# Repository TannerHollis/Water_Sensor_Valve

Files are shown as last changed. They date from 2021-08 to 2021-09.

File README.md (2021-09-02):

# Water Sensor Valve
 This project mimics the operation of a "Water Cop". While commercial use of this device is expensive, a simple cheap clone can be replicated for a mere dollars.
 
## Water Sensor
The water sensor is a simple wheatstone bridge with one leg of the resistor divider being the exposed metal strips in the probe. Due to variation in the installation of the product, the probe's resistivity will change. Using a wide variety of different possible probe gaps, the wheatstone bridge is configurable for up to 15 different resistor combinations. See [total_resistor_combinations.txt](https://github.com/TannerHollis/Water_Sensor_Valve/blob/main/Water_Valve_Calculations/total_resistor_combinations.txt) for all possible combinations. The purpose of this configuration is to accomodate for a wide range of possible probe resistivities.

A "dirty" or water typically found with contamination in it widely varies in it's resistivity, or it's ability to conduct electricity. Since the resistivity of air is magnitudes larger than the resistivity of water, the effect on the probes open air contacts can be ignored for the theoretical calculations. 

Contaminated water has a resitivity typically between 20 to 2000 Ohms. To calculate the theoretical resistance between two electrical wires submerged in water, one must utilize the resistance formula.

	R = p L / A
 
This device is meant to be used with a probe with a small 2mm gap and approximately 31um^2 of exposed contacts on the probe, which when submerged in conductive water yields a theoretical maximum resistance of ~127 kOhms. Tolerances must be added to assure the proper resistivity is measured. In this scenario, we would recommend using a setting of 84.777 kOhms which corresponds to jumping resistors R3 and R4 corresponding to 127 and 255 kOhm resistors. At this set point, any measured resistance below the threshold of 84.777 kOhms will trigger the closing of the valve and sounding of the alarm.

Adjustments may be needed for more sensitivity or security. For more sensitivity, refer to the resistor combination file and choose the next highest setting. For more security,  choose the next lowest setting. Continue to do so until the desired operation is achieved. 

## Custom Setting Attachment
This add-on is a customizable attachment that is configurable with either the use the included potentiometer or the solderable resistor footprint. With the included mosfet, an external controller can be attached and control the Water Sensor Valve using the connections with the use of the included external mosfet.

- [X] Test and verify first revision
- [X] Verify alarm and valve operation
- [ ] Design and print custom device housing
- [ ] Create custom setting attachment
- [ ] Control device with custom setting attachment using MCU
- [ ] Setup configurable custom setting attachement using potentiometer

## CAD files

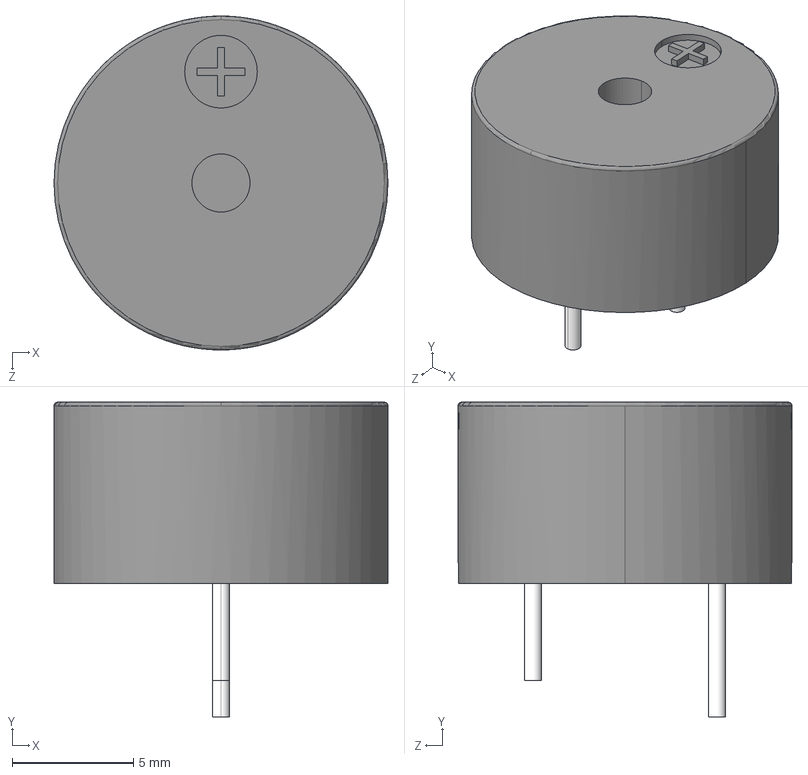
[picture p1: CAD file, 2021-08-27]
Water_Valve_Sensor/Parts/CUI_DEVICES_CPI-1375IC-80T.step
13.8 x 13.0 x 13.8 mm

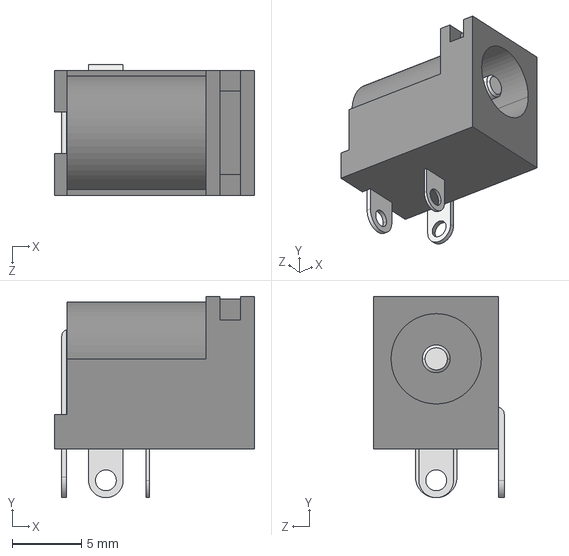
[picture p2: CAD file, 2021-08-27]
Water_Valve_Sensor/Parts/CUI_DEVICES_PJ-002A.step
14.4 x 14.5 x 9.40 mm

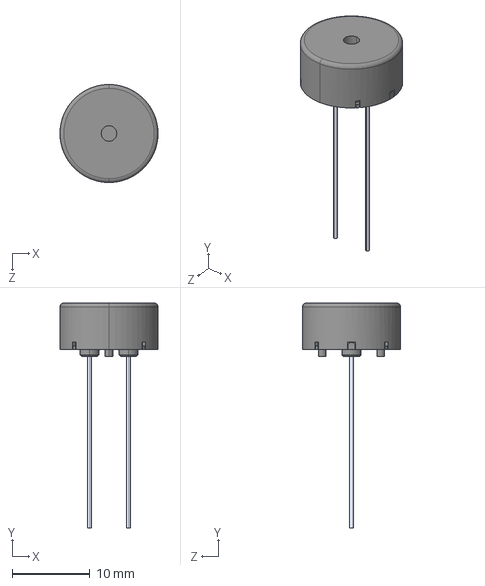
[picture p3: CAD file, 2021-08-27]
Water_Valve_Sensor/Parts/PKM13EPYH4000-A0.step
12.6 x 28.9 x 12.6 mm

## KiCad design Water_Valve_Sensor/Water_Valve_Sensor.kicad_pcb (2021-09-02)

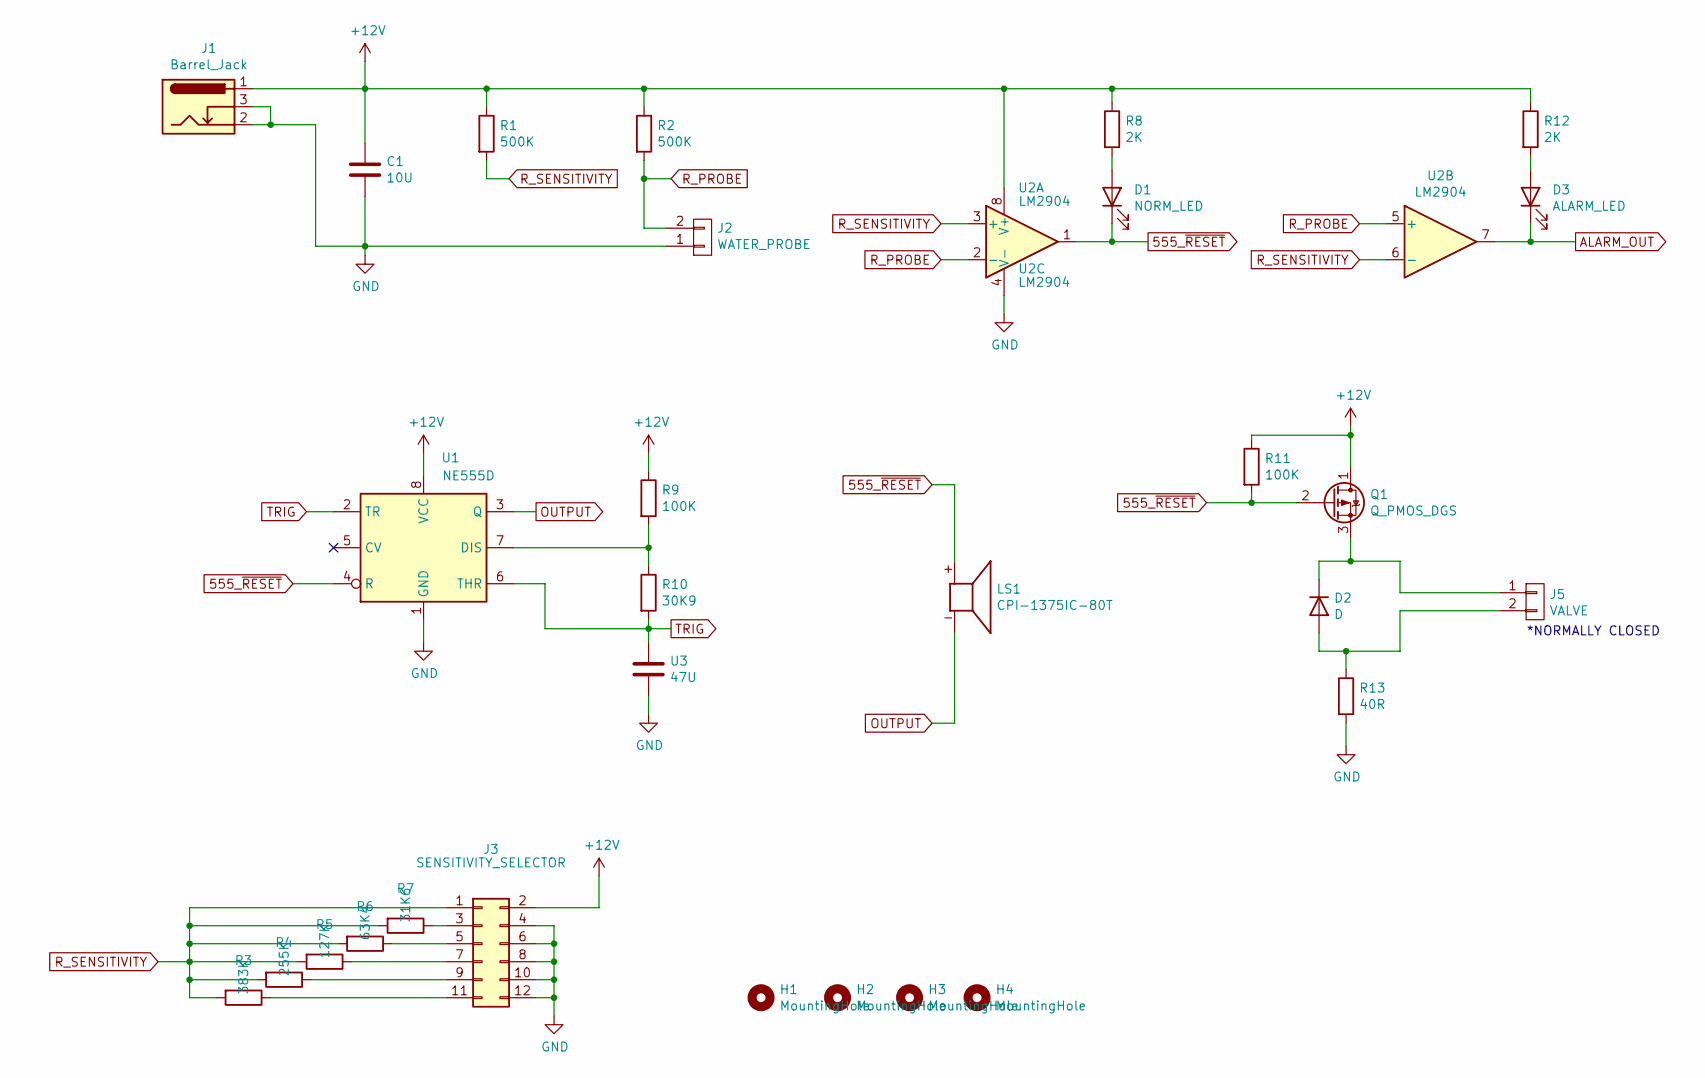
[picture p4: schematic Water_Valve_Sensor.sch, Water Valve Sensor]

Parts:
C1: 10U; CP_Radial_D5.0mm_P2.00mm
D1: NORM_LED; LED_D3.0mm
D2: D; D_DO-15_P10.16mm_Horizontal
D3: ALARM_LED; LED_D3.0mm
H1, H2, H3, H4: MountingHole; MountingHole_2.5mm_Pad_TopBottom
J1: Barrel_Jack; PJ-002A
J2: WATER_PROBE; PinHeader_1x02_P2.54mm_Horizontal
J3: SENSITIVITY_SELECTOR; PinHeader_2x06_P2.54mm_Vertical
J5: VALVE; PinHeader_1x02_P2.54mm_Horizontal
LS1: CPI-1375IC-80T; CUI_CPI-1375IC-80T; PARTREV 1.0
Q1: Q_PMOS_DGS; TO-92
R1, R2: 500K; R_Axial_DIN0207_L6.3mm_D2.5mm_P7.62mm_Horizontal
R3: 383K; R_Axial_DIN0207_L6.3mm_D2.5mm_P7.62mm_Horizontal
R4: 255K; R_Axial_DIN0207_L6.3mm_D2.5mm_P7.62mm_Horizontal
R5: 127K; R_Axial_DIN0207_L6.3mm_D2.5mm_P7.62mm_Horizontal
R6: 63K4; R_Axial_DIN0207_L6.3mm_D2.5mm_P7.62mm_Horizontal
R7: 31K6; R_Axial_DIN0207_L6.3mm_D2.5mm_P7.62mm_Horizontal
R8, R12: 2K; R_Axial_DIN0207_L6.3mm_D2.5mm_P7.62mm_Horizontal
R9, R11: 100K; R_Axial_DIN0207_L6.3mm_D2.5mm_P7.62mm_Horizontal
R10: 30K9; R_Axial_DIN0207_L6.3mm_D2.5mm_P7.62mm_Horizontal
R13: 40R; R_Axial_DIN0207_L6.3mm_D2.5mm_P7.62mm_Horizontal
U1: NE555D; SOIC-8_3.9x4.9mm_P1.27mm
U2: LM2904; SOIC-8_3.9x4.9mm_P1.27mm
U3: 47U; CP_Radial_D5.0mm_P2.00mm

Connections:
555_~RESET~: D1.1 (K), LS1.P, Q1.2 (G), R11.2, U1.4 (R), U2.1
+12V: C1.1, J1.1, J3.2, Q1.1 (D), R1.1, R2.1, R8.1, R9.1, R11.1, R12.1, U1.8 (VCC), U2.8 (V+)
ALARM_OUT: D3.1 (K), U2.7
GND: C1.2, J1.2, J1.3, J2.1, J3.4, J3.6, J3.8, J3.10, J3.12, R13.2, U1.1 (GND), U2.4 (V-), U3.2
unnamed: D1.2 (A), R8.2
unnamed: D2.1 (K), J5.1, Q1.3 (S)
unnamed: D2.2 (A), J5.2, R13.1
unnamed: D3.2 (A), R12.2
unnamed: J3.3, R7.1
unnamed: J3.5, R6.1
unnamed: J3.7, R5.1
unnamed: J3.9, R4.1
unnamed: J3.11, R3.1
unnamed: R9.2, R10.1, U1.7 (DIS)
OUTPUT: LS1.N, U1.3 (Q)
R_PROBE: J2.2, R2.2, U2.2 (-), U2.5 (+)
R_SENSITIVITY: J3.1, R1.2, R3.2, R4.2, R5.2, R6.2, R7.2, U2.3 (+), U2.6 (-)
TRIG: R10.2, U1.2 (TR), U1.6 (THR), U3.1

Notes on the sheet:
*NORMALLY CLOSED

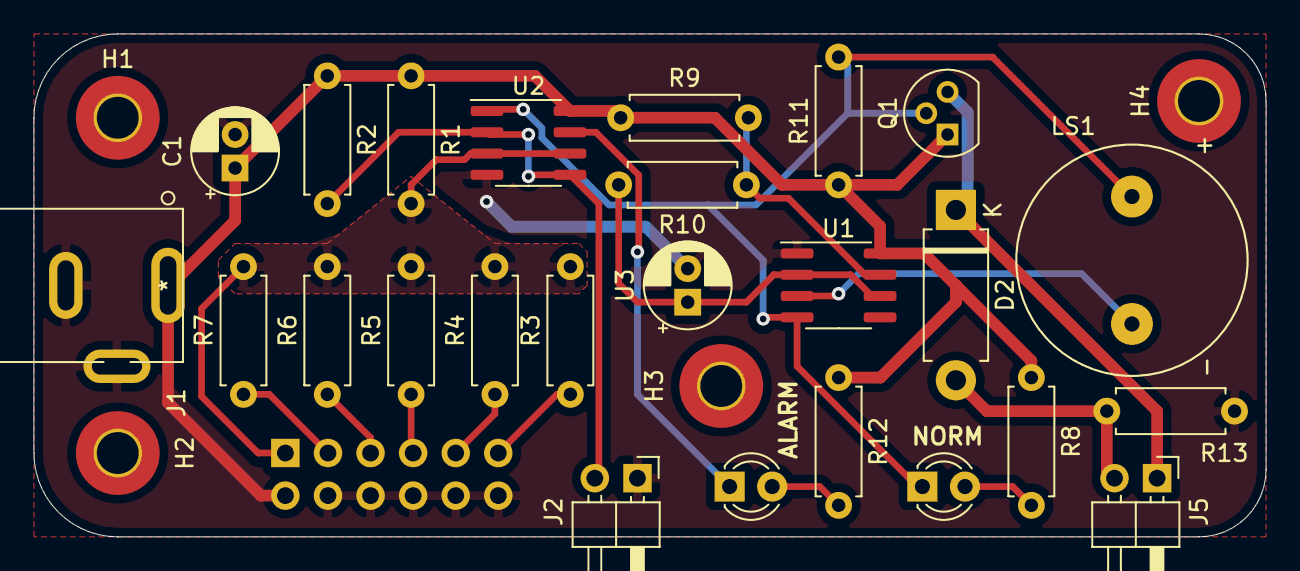
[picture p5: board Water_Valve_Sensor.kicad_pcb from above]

Board: 2 copper layers, 73.5 x 30.0 mm, 30 parts (1 on the bottom side), 18 nets.

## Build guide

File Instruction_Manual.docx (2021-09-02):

# Water Sensor Valve Instructions

Offset Power, Inc.

### Phone: (704) - 999 -3983

Email: hollis.tanner@gmail.com

This device is intended to be used in areas where access to leaking waterlines or faucets is not easily accessible. When the device’s probes encounter water or a conductive liquid, the device will alarm and close the water valve, preventing water damage to the surrounding area. Included in this package are the following contents:

| Item | Description
1x | Wall adapter | 12V, 6W AC-DC Wall Adapter
1x | Water Sensor Device | Water Sensor Device
1x | Solenoid Valve | 12V, 250mA Normally Closed (NC) Valve
1x | Water Probe | Water Sensor Probe, 2mm Gap
5x | Sensitivity Jumpers | Sensitivity Selector Jumpers

# Easy Setup Instructions

## Ensure the normal operation of the device

1. Locate a nearby wall outlet nearest to the desired location and plug-in the wall adapter.
2. Connect the barrel jack into the device and the green light should light to indicate that the device is powered-on and working normally.
3. Connect the valve into the device before installing the water valve in place.
4. Connect the water probe into the device and keep the probe’s sheaths on.
5. If not connected, connect a single Sensitivity Jumper in position 1 (Fig. 1).

## Test the Device

1. Remove the probe’s rubber sheath and test the probe by dipping it into water or by wetting one’s finger tips and squeezing the probe.
2. The device’s normal LED should turn-off and the alarm LED should turn-on.
3. The valve should close and the alarm should sound.
4. The alarm will sound for approximately 1 second and turn-off for 3.5 seconds.
5. If this sequence is not heard, continue to sensitivity tuning is properly done before continuing troubleshooting.

## Sensitivity Tuning

This device is intended to operate in a wide variety of conditions. For instance, placing this device in a damp and cool place may cause a misoperation due to very high air humidty. To ensure proper functionality, please follow these steps:

1. Start with a single Sensitivity Jumper in position 1 (Fig. 1)
2. Test the probe by dipping it into water or squeezing between wet fingers.
3. Continue to move the single Sensitivity Jumper up into the next position until the device does not function properly.
  a. If you reach position 5 and the device still operates, please refer sensitivity chart (Fig. 2) and move up to make the device more sensitive. If the device does not operate after moving up to the top of the chart please refer to the support line and a custom custom solution will be created to suite your needs.
4. If you have reached a position where the device does not operation, you should note position that did not yield proper functionality.
5. From this position, you can refer to the sensitivity chart and move down the chart until the device operates again.
6. When the device operates again, please add sensitivity or security to one’s desired effectiveness and continue to test until the desired outcome is achieved.

## Sensitivity Chart

| 5 | 4 | 3 | 2 | 1 | Resistance (Ω)
Configuration 15 | 1 | 1 | 1 | 1 | 1 | 16174.68
Configuration 14 | 1 | 1 | 1 | 1 | 0 | 16887.89
Configuration 13 | 1 | 1 | 1 | 0 | 0 | 18085.64
Configuration 12 | 1 | 1 | 0 | 0 | 0 | 21088.84
Configuration 11 | 1 | 0 | 0 | 0 | 0 | 31600.00
Configuration 10 | 0 | 1 | 1 | 1 | 1 | 33135.16
Configuration 9 | 0 | 1 | 1 | 1 | 0 | 36273.34
Configuration 8 | 0 | 1 | 1 | 0 | 0 | 42288.86
Configuration 7 | 0 | 1 | 0 | 0 | 0 | 63400.00
Configuration 6 | 0 | 0 | 1 | 1 | 1 | 69412.86
Configuration 5 | 0 | 0 | 1 | 1 | 0 | 84777.48
Configuration 4 | 0 | 0 | 1 | 0 | 0 | 127000.00
Configuration 3 | 0 | 0 | 0 | 1 | 1 | 153079.93
Configuration 2 | 0 | 0 | 0 | 1 | 0 | 255000.00
Configuration 1 | 0 | 0 | 0 | 0 | 1 | 383000.00

How to Read:

By default, the device is shipped with a jumper in position 1. In this position, the device is most sensitive. “Moving up” in the chart means decreasing sensitivity and increasing security. To do so, one must either remove or add additional jumpers into corresponding positions to achieve the next setting in the chart.

Example:

Moving from Configuration 1 to Configuration 9.

1. Remove the jumper from position 1 and place the jumper into position 2.
2. Place additional jumpers into positions 2, and 3.
3. The result should match the figure below (Fig. 3).
4. The new configuration is now less sensitive and more secure. This configuration might be used in very damp climates where AC is not provided to the room where this device will operate.

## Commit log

2021-08-27 Deleted Files
    Deleted Files
    [CUI_DEVICES_PJ-002A.step]
2021-08-30 Fixed Wiring Issue
    Added support for 2x6 header for Custom Setting Attachment
    [Water_Valve_Sensor.kicad_pcb, Water_Valve_Sensor.sch]
2021-08-31 Updated Resistor Combination
    Updated Resistor Combination
    [Water_Valve_Sensor.kicad_pcb]
2021-09-02 Changes to resistor selections
    Updated sensitivty resistors.
    [Water_Valve_Sensor.kicad_pcb, Water_Valve_Sensor.sch]

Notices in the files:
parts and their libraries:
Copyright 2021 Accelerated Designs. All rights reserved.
